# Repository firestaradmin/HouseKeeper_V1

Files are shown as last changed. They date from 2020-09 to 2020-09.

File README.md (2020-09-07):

@[TOC](导航)

---
**本项目已开源至GitHub：*[点我传送](https://github.com/firestaradmin/HouseKeeperV1)***

---
# 一、HouseKeeperV1.0介绍
### 1.项目简介：

 - HouseKeeper_V1.0  是一款智能物联家居产品，它可以根据需求方便的扩展各种家居家电控制，例如门的控制，窗帘的控制，和一些其他家电的控制，只需要简单外接一个继电器便可。本次我们将用指纹门锁控制，来阐述HouseKeeper的功能。
### 2.项目图片外观实例：
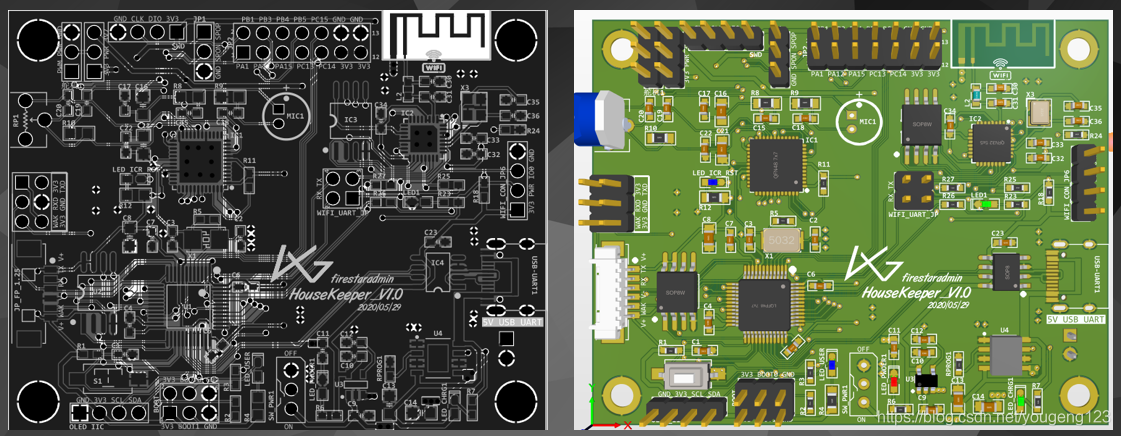
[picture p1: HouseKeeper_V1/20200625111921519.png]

##### · 初步产品图如下
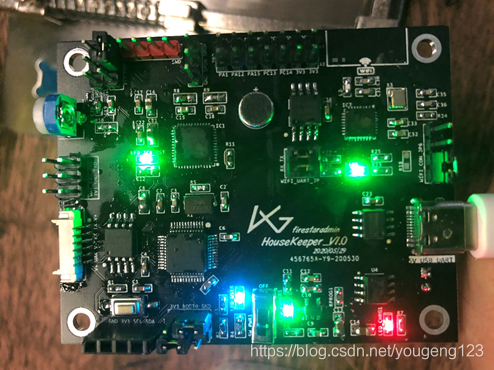
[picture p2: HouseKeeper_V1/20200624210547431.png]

##### · 指纹门锁实例图
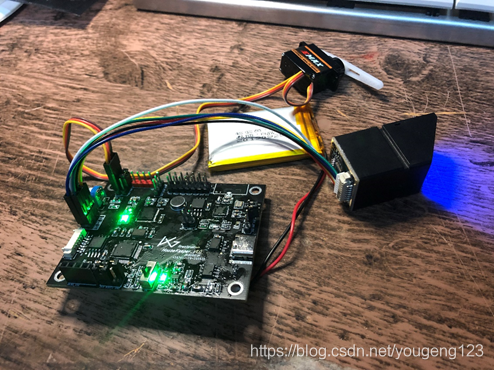
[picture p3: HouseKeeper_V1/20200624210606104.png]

### 3.项目板载资源及功能介绍：
 - 本次项目PCB使用STM32F103C8T6作为主控芯片，板载了WIFI和LD3320语音识别芯片。 有板载麦克风，和0.5W的扬声器输出。
   PCB周边具有舵机接口，指纹模块接口，和将近十个IO扩展，可方便的扩展其他应用。
   另外Type-C的usb串口供电二合一，很方便产品开发阶段使用。

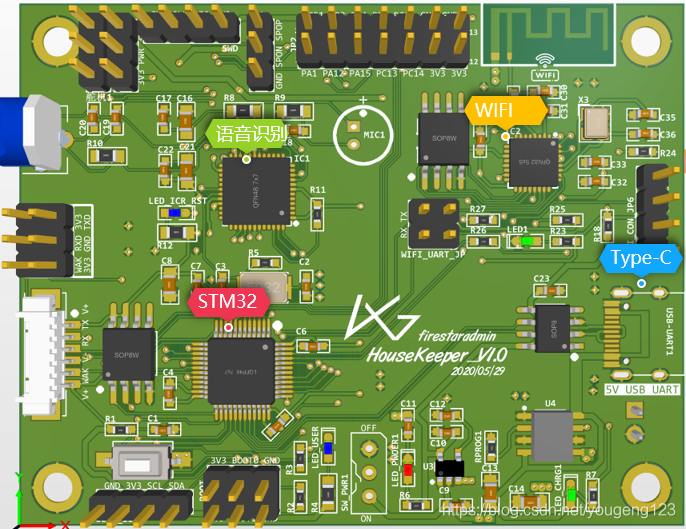
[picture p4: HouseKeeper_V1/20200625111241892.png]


 - 板载资源：
MCU：STM32F103
SPI-FLASH：	W25Q64-8MB
WIFI：ESP8266EX
语音识别： LD3320
锂电池电源管理：TP4056
等等

# 二、HouseKeeperV1.0部分原理图
### 1.主控部分：
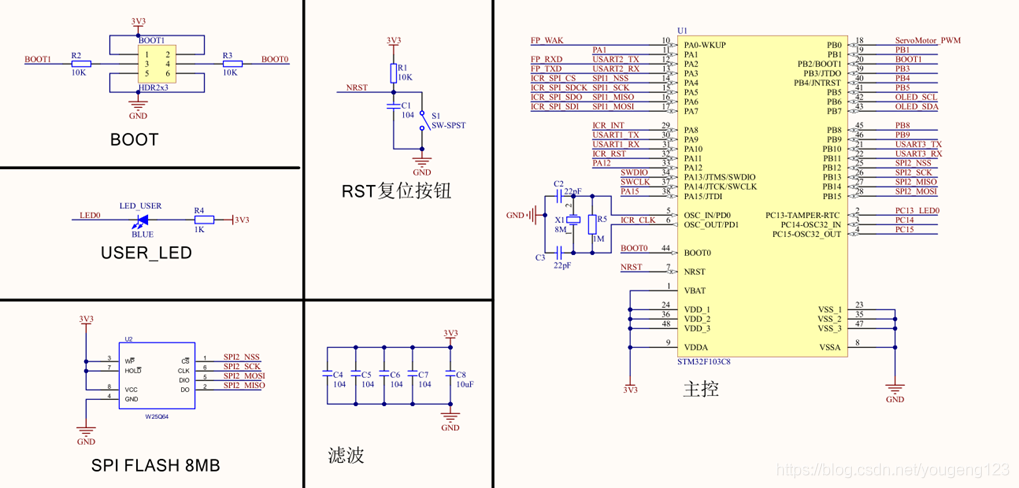
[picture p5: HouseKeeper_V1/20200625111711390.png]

### 2.ESP8266EX-WIFI部分：
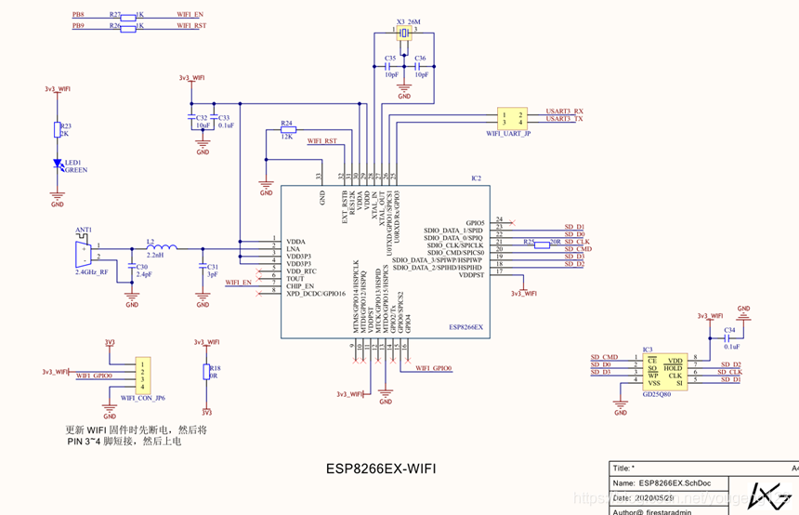
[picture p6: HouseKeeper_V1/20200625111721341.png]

### 3.LD3320语音识别部分：
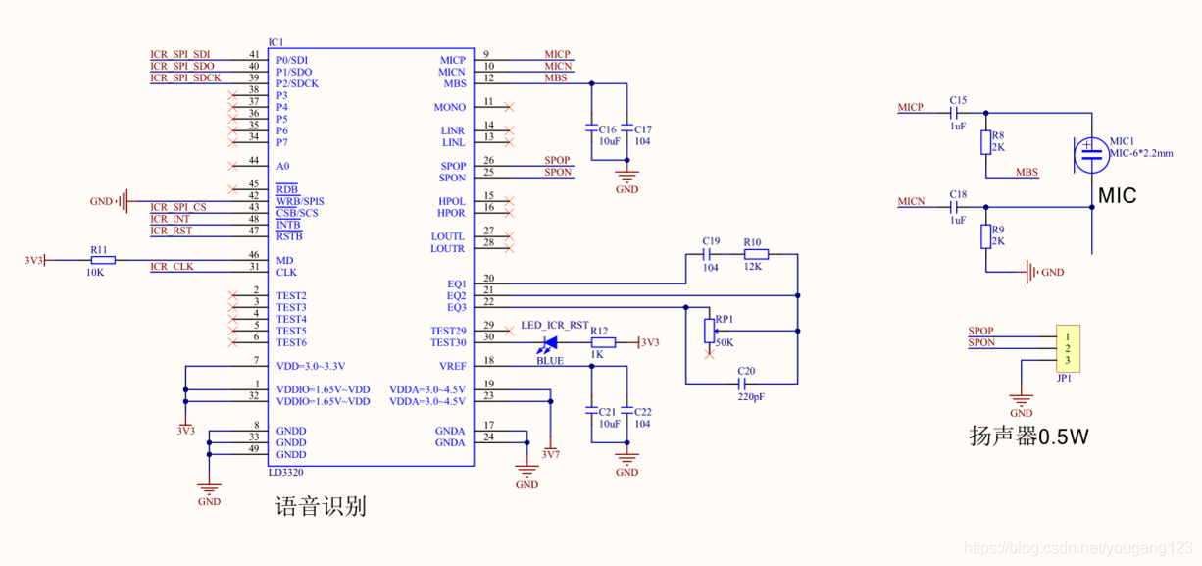
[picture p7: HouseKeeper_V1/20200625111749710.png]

# 三、基于HouseKeeperV1.0的案例-物联网指纹门锁

 - 程序会识别指纹id，判断是谁开了门，并且实时更新到云服务器上的数据库中。 QT中可以实时查看到服务器数据库的信息。

### 1.基础流程图：
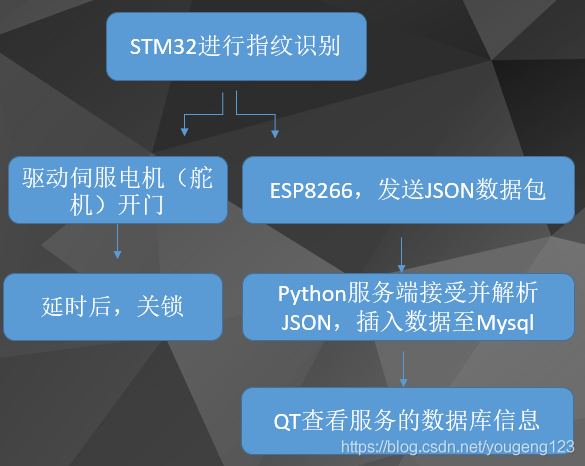
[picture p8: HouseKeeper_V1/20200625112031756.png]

### 2.软件部分框架：
 - 主控程序使用keil编写STM32—C程序
 - WIFI固件，采用arduino编写C++程序
 - 服务器后台使用Python编写SOCKET TCP服务程序
 - 服务器部署了Mysql数据库用于记录开门信息
 - 上位机查看数据库使用QT-C++编写
##### 1.ESP8266WIFI固件功能：
 - 首先连接指定WIFI，循环检查连接状态 如果接受到了，主控发送来的指纹ID，说明该ID开了门 
 - 使用socket连接服务器Serve端。 发送指定格式的JSON数据包，根据ID识别是某位开的门，上传不同的信息

 - **JSON数据包格式：”{“opreation”:“close”, “Note”:“firestaradmin”}”**
##### 2.Python服务端功能：

 - 使用socket 建立TCP服务器，等待Client的连接。
 - 如果有数据接收到，就进行JSON解析，如果正确，无缺失内容，则和系统时间，一起插入至Mysql数据库。
 - 接受客户端发送JSON数据包并解析，解析成功后讲数据插入Mysql数据库

### 3.实例开发过程的一些图片：
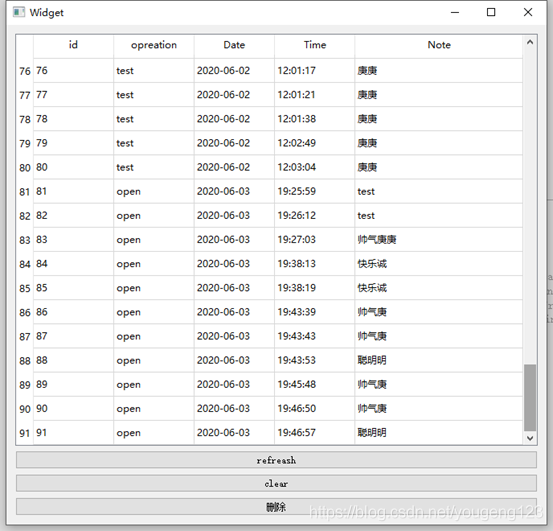
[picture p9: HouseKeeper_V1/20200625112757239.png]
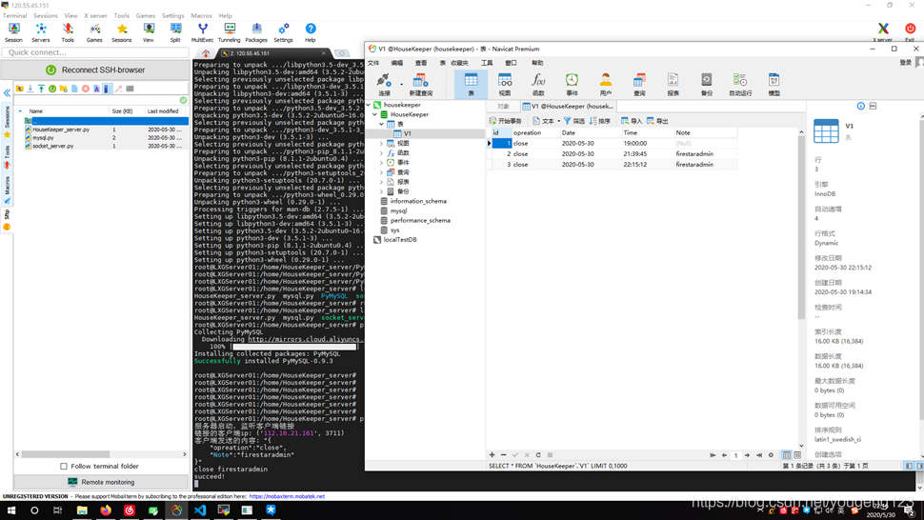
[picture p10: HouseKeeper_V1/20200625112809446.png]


 - 具体演示视频已上传至GitHub项目文件下的report文件夹下，可一起下载后观看

# 四、制作过程部分图片
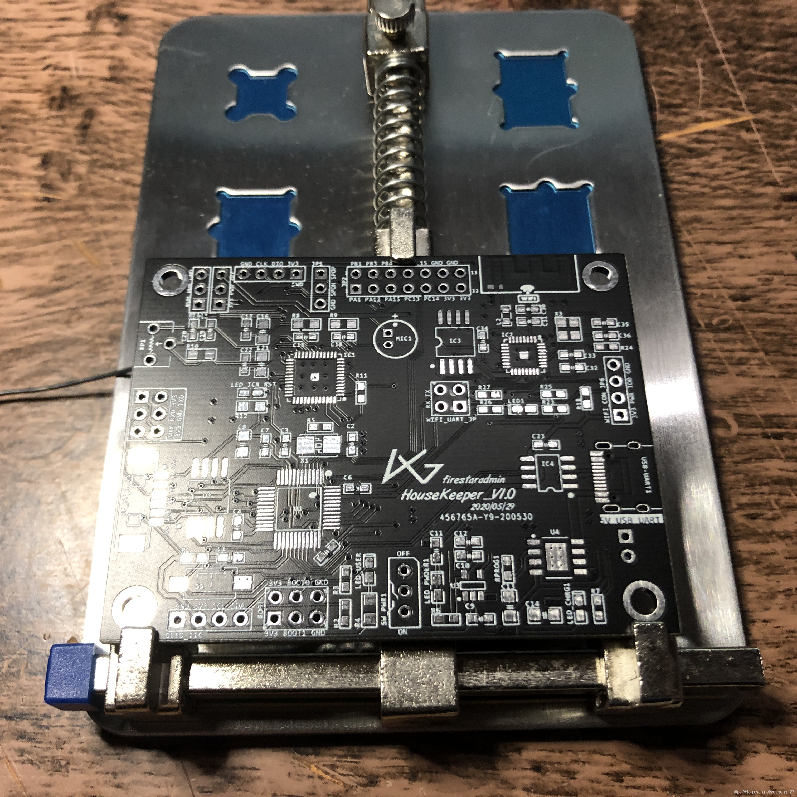
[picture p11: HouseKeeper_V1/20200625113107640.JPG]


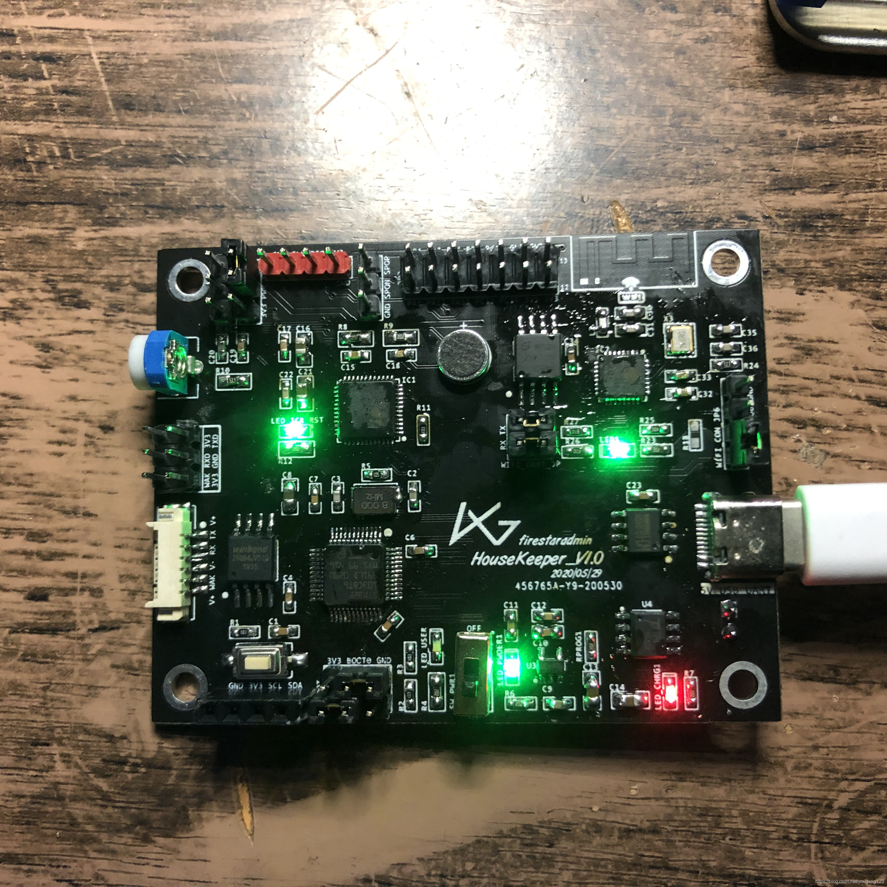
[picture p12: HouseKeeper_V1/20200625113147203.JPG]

在这里插入图片描述
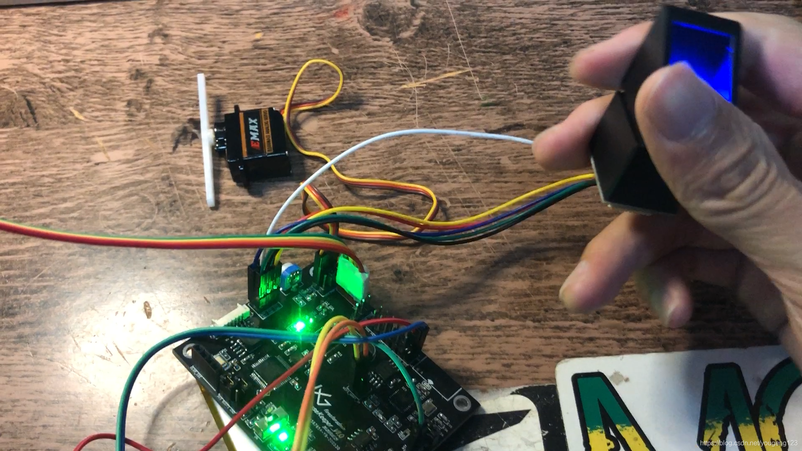
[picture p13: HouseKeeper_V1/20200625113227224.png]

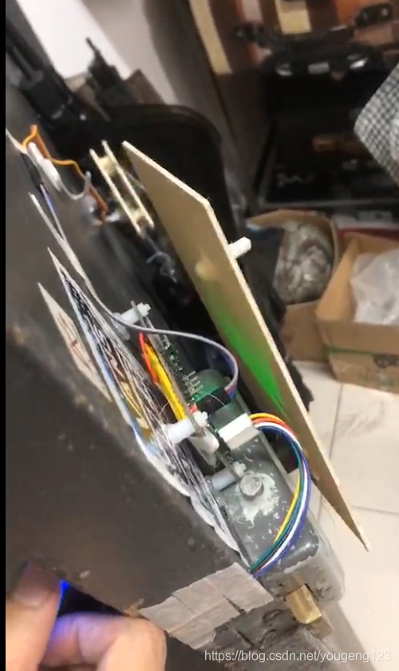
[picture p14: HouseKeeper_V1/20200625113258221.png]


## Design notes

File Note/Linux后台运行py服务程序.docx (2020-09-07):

## &符号

这两天要在服务器端一直运行一个Python脚本，当然就想到了在命令后面加&符号
$ python /data/python/server.py >python.log &

说明：
1、 > 表示把标准输出（STDOUT）重定向到 那个文件，这里重定向到了python.log
2、 & 表示在后台执行脚本
这样可以到达目的，但是，我们退出shell窗口的时候，必须用exit命令来退出，否则，出之后，该进程也会随着shell的消失而消失（退出、关闭）

## 使用nohup(not hang up)

$ nohup python /data/python/server.py > python.log3 2>&1 &

说明：
1、1是标准输出（STDOUT）的文件描述符，2是标准错误（STDERR）的文件描述符
1> python.log 简化为 > python.log，表示把标准输出重定向到python.log这个文件
2、2>&1 表示把标准错误重定向到标准输出，这里&1表示标准输出
为什么需要将标准错误重定向到标准输出的原因，是因为标准错误没有缓冲区，而STDOUT有。
这就会导致 commond > python.log 2> python.log 文件python.log被两次打开，而STDOUT和 STDERR将会竞争覆盖，这肯定不是我门想要的
3、好了，我们现在可以直接关闭shell窗口（我用的是SecureCRT，用的比较多的还有Xshell），而不用再输入exit这个命令来退出shell了

command &让进程在后台运行

jobs 查看后台运行的进程

fg %n 让后台运行的进程n到前台来

bg %n 让进程n到后台去

kill %n 杀死job

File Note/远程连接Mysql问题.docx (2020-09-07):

## Mysql 监听ip地址修改

Mysql默认在本地环路地址127.0.0.1的3306端口监听，要使用其它IP地址需要修改配置文件。

1.编辑/etc/my.cnf 在[mysqld]节中增加下面一行：

bind-address=0.0.0.0 #全部地址或者指定的ip地址

2.重启服务

service mysqld restart

3.验证

netstat -tln

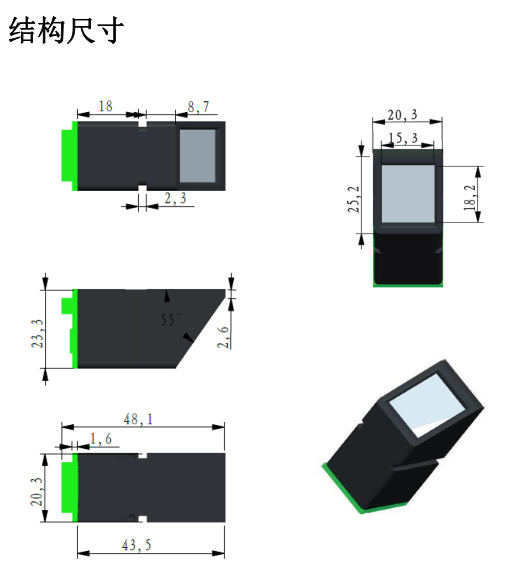
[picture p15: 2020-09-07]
DOC/YX66318-AS608指纹模块-190520/结构图.png

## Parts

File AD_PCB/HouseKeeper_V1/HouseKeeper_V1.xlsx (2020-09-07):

Comment | Description | Designator | Footprint | Quantity
104 | Capacitor, 无极性贴片电容 | C1, C4, C5, C6, C7, C10, C17, C19, C22 | C 0603_M | 9
10uF | 无极性贴片电容, Capacitor | C8, C13, C14, C16, C21 | C 0805_M | 5
1K | 贴片电阻, Resistor | R6, R7, R26, R27 | R 0603_M | 4
10K |  | R1, R2, R3, R11 | R 0603_M | 4
Comment |  | Designator1, Designator10 | M3 125X200 | 4
0.1uF | 无极性贴片电容 | C23, C33, C34 | C 0603_M | 3
HDR-1X3 | 3P接插件 | JP1, JP3, 舵机1 | HDR2.54-LI-3P | 3
1K | 贴片电阻 | R4, R12 | R 0805_M | 2
1uF | 无极性贴片电容 | C15, C18 | C 0603_M | 2
2K | Resistor | R23, RPROG1 | R 0603_M | 2
2K | 贴片电阻 | R8, R9 | R 0805_M | 2
10pF | 无极性贴片电容 | C35, C36 | C 0603_M | 2
22pF | Capacitor | C2, C3 | C 0603_M | 2
105 | Capacitor | C9, C11 | C 0603_M | 2
BLUE | 贴片LED | LED_ICR_RST, LED_USER | LED 0603B | 2
0R | Resistor | R18 | R 0603_M | 1
1M | 贴片电阻 | R5 | R 0603_M | 1
2.2nH | 小功率贴片电感 | L2 | L 0603 | 1
2.4GHz_RF |  | ANT1 | ANT-F-1-2.4G | 1
2.4pF | 无极性贴片电容 | C30 | C 0603_M | 1
3pF | 无极性贴片电容 | C31 | C 0603_M | 1
8M | Crystal Oscillator | X1 | OSC 5032-2P | 1
10uF | 无极性贴片电容 | C32 | C 0603_M | 1
12K | Resistor | R24 | R 0603_M | 1
12K | 贴片电阻 | R10 | R 0805_M | 1
20R | Resistor | R25 | R 0603_M | 1
22nf | Capacitor | C12 | C 0603_M | 1
26M | 4脚无源晶振 | X3 | OSC 3225-4P | 1
50K | 插件单联电位器 | RP1 | 3306W | 1
220pF | 无极性贴片电容 | C20 | C 0603_M | 1
CH340N | USB 转串口芯片 CH330/CH340N | IC4 | SOP8_N | 1
ESP8266EX | WIFI-芯片 | IC2 | QFN32 5x5_M | 1
GD25Q80 | 外置Flash | IC3 | SOP8W_N | 1
GREEN | 贴片LED | LED1 | LED 0603G | 1
HDR1x2 | Connector | 4.2V锂电池 | XH2.54-LI-2P | 1
HDR2x3 | Connector | BOOT | HDR2.54-LI-2x3P | 1
HDR-1X4 | 4P接插件 | WIFI_CON_JP6 | HDR2.54-LI-4P | 1
HDR-1X6 | 6P接插件 | JP_FP_1.25 | MX 1.25-WS-6P | 1
HDR-1X6 | 6P接插件 | JP_FP_2.54 | HDR2.54-LI-2x3P | 1
Header2X2 | 2*2P接插件 | WIFI_UART_JP | HDR2.54-LI-2x2P | 1
Header 2X7 | 7*2P接插件 | JP2 | HDR2.54-LI-2x7P | 1
LD3320 | LD3320 芯片是一款“ 语音识别”专用芯片，由 ICRoute 公司设计生产。该芯 片集成了语音识别处理器和一些外部电路，包括 AD、DA 转换器、麦克风接口、 声音输出接口等。本芯片在设计上注重节能与高效，不需要外接任何的辅助芯片 如 Flash、RAM 等，直接集成在现有的产品中即可以实现语音识别/声控/人机对 话功能。并且，识别的关键词语列表是可以任意动态编辑的。 | IC1 | QFN48 7X7_M | 1
LED | LED | LED_CHRG1 | LED 0603G | 1
MIC-6*2.2mm | 电容麦克风 | MIC1 | MIC-6*2.2MM | 1
OLED | Header, 4-Pin | OLED_IIC | HDR2.54-LI-4P | 1
RED | 贴片LED | LED_PWOER1 | LED 0603R | 1
RT9193 |  | U3 | SOT-23-5 | 1
STM32F103C8 | Flaah:64/RAM:20/IO:36 | U1 | LQFP48 7X7_M | 1
SWD | Header, 4-Pin | SWD | HDR2.54-LI-4P | 1
SWITCH-SPST | Switch | SW_PWR1 | Switch_3p_2.5mmjianju | 1
SW-SPST | Single-Pole, Single-Throw Switch | S1 | TSW SMD-3*6*2.5 | 1
TP4056 |  | U4 | ESOP8 | 1
Type-C |  | USB-UART1 | TYPE-C | 1
W25Q64 |  | U2 | SOP8W_M | 1

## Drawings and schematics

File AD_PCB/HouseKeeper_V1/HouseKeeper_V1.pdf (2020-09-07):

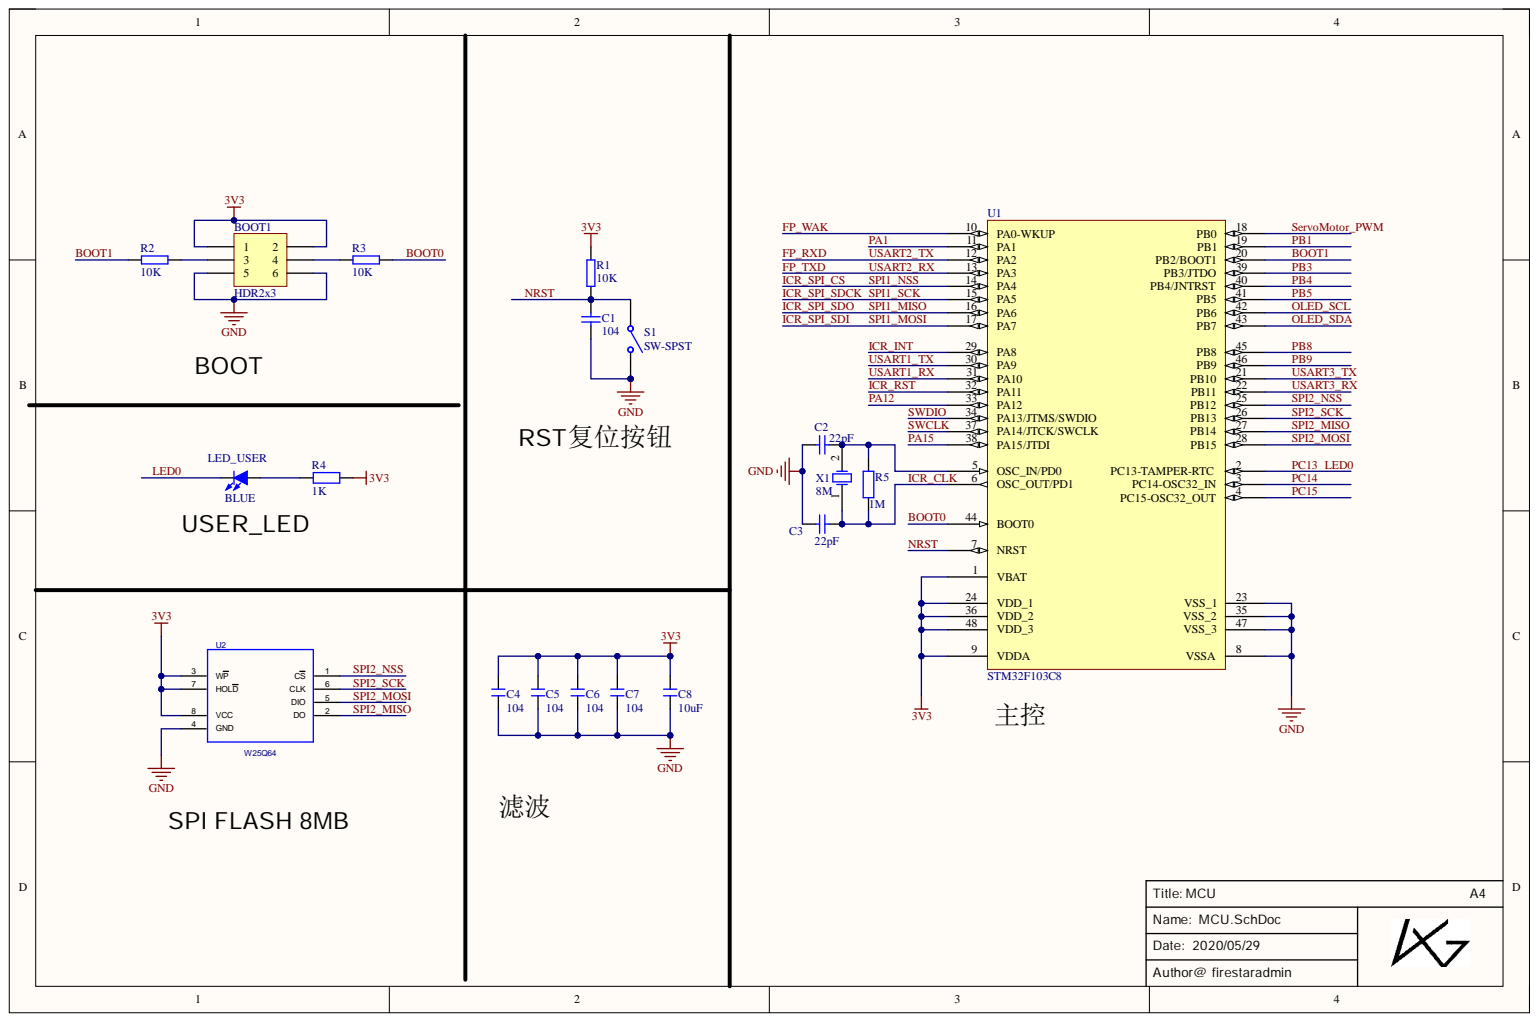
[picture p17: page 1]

ICR_CL K 6

2 4
3 6 | 3 5
4 8 | | 4 7

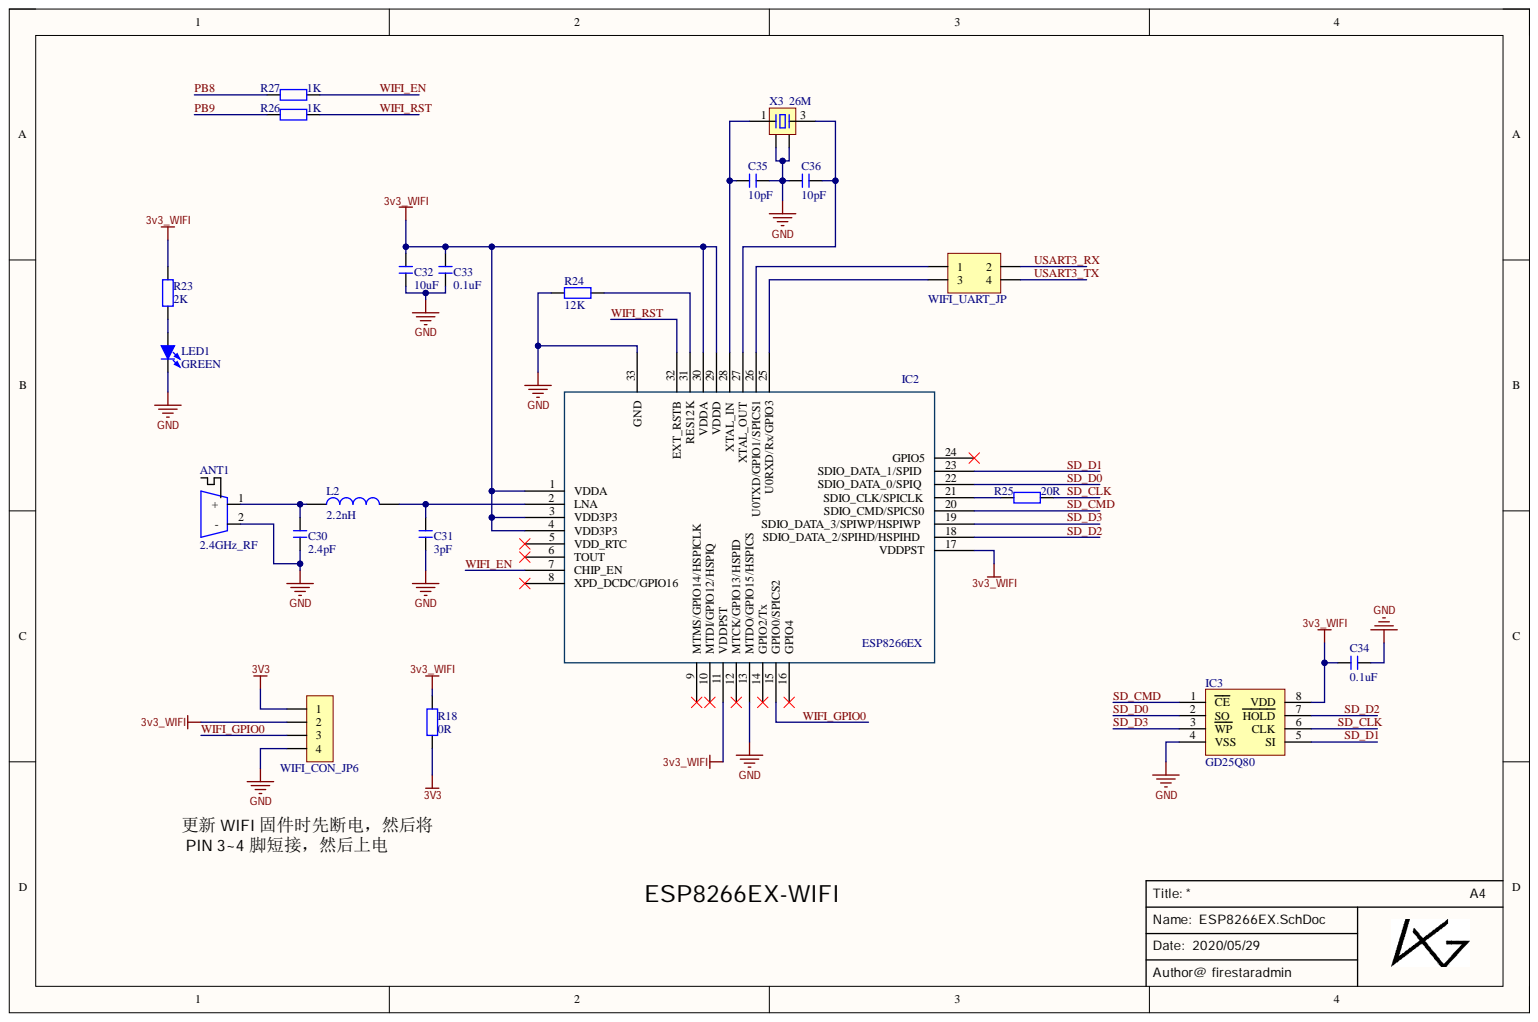
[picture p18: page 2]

更新 WIFI 固件时先断电，然后将
PIN 3~4 脚短接，然后上电

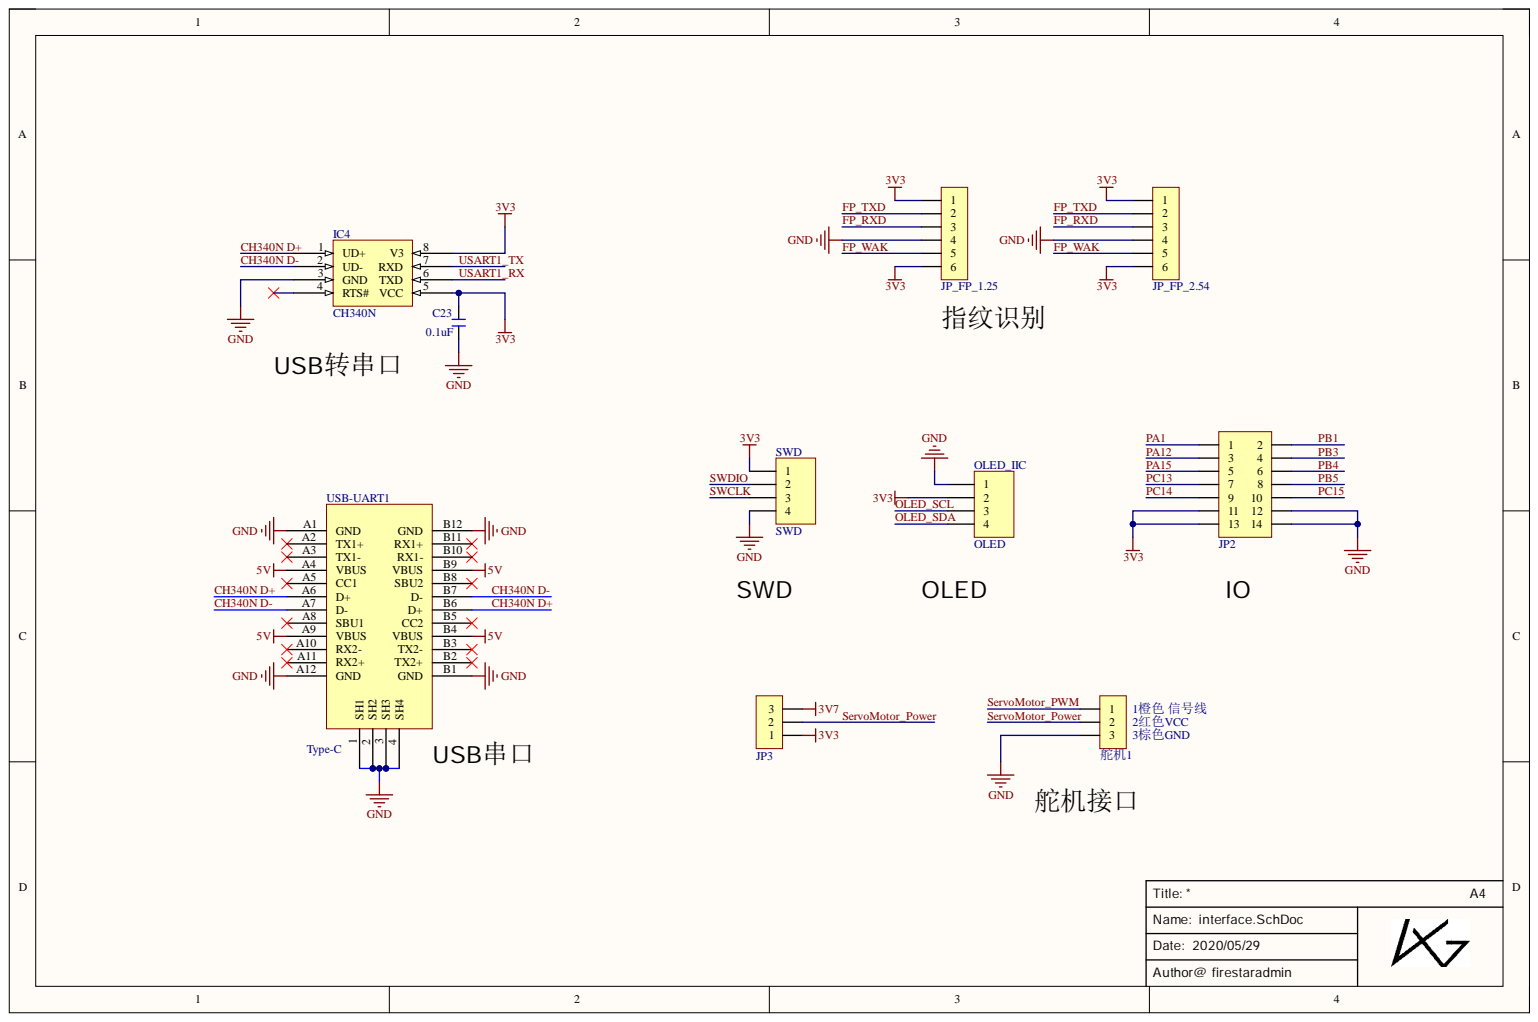
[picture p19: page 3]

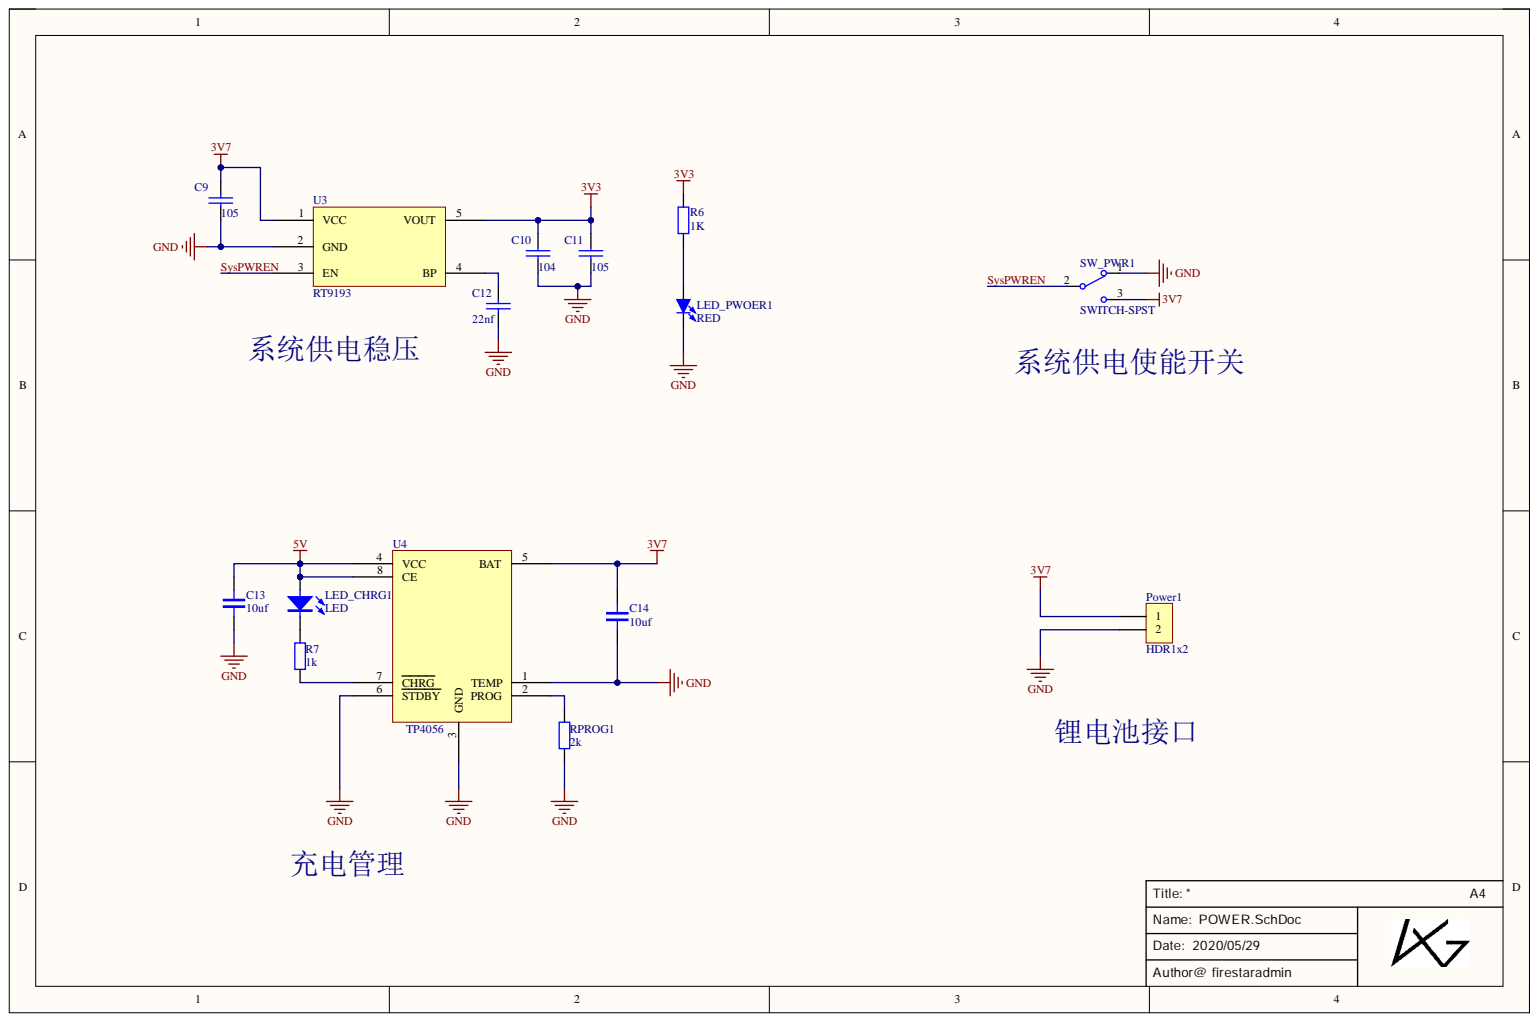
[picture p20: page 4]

STDBY 6

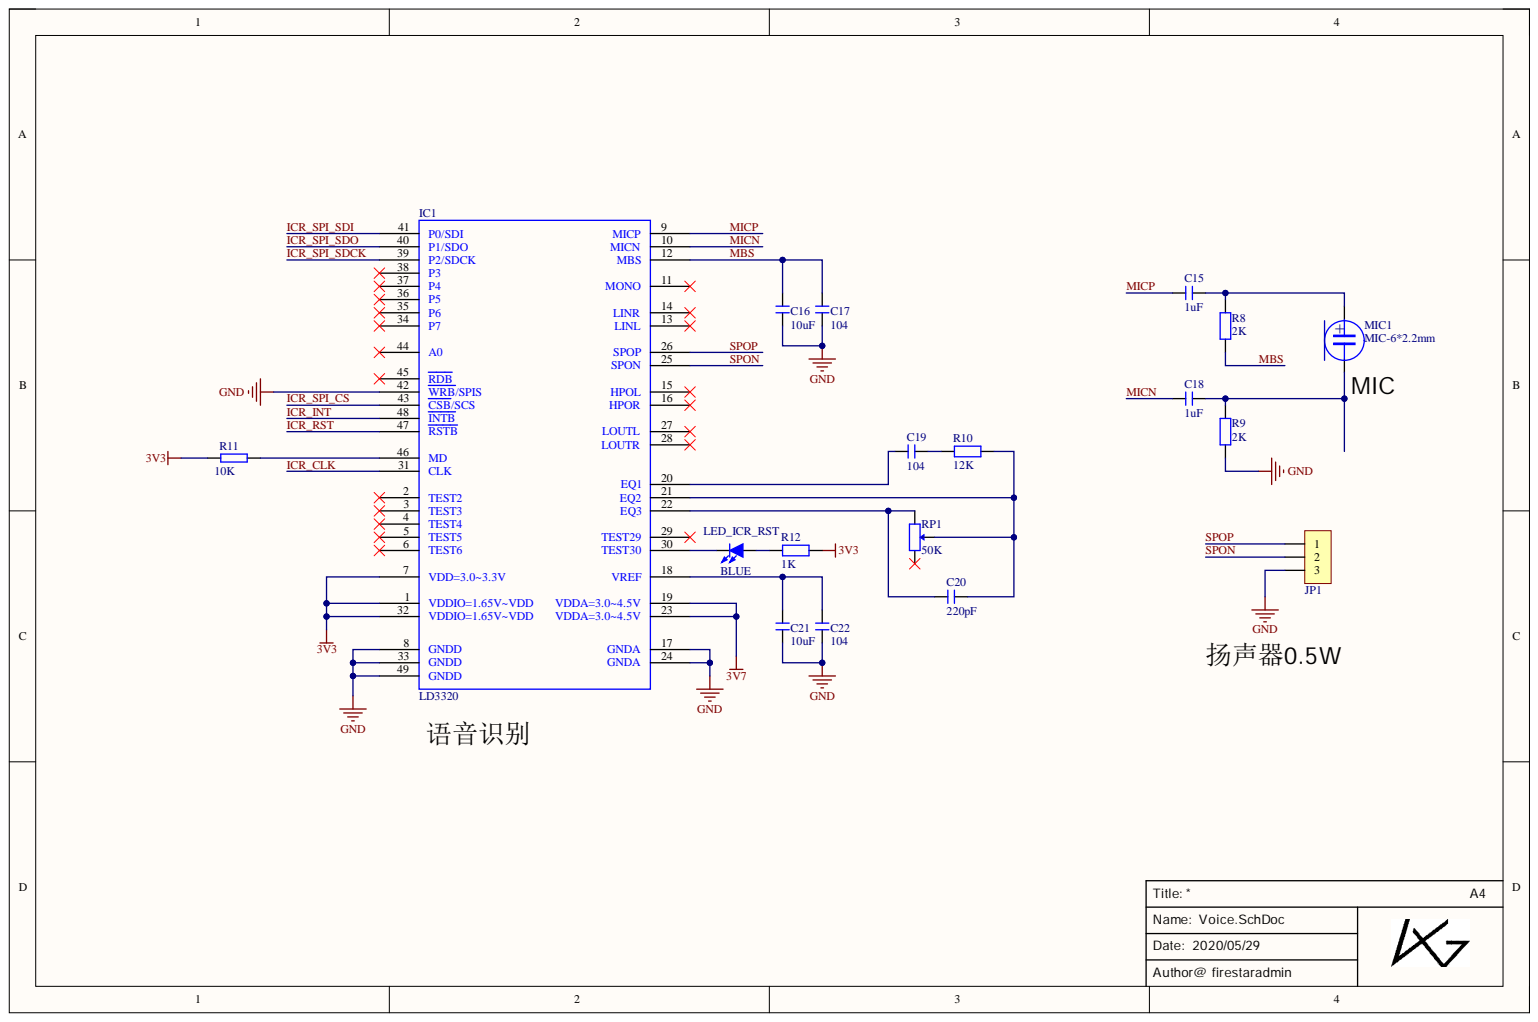
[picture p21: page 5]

1 | 1 9
3 2 | 2 3

3 3 | 2 4
4 9

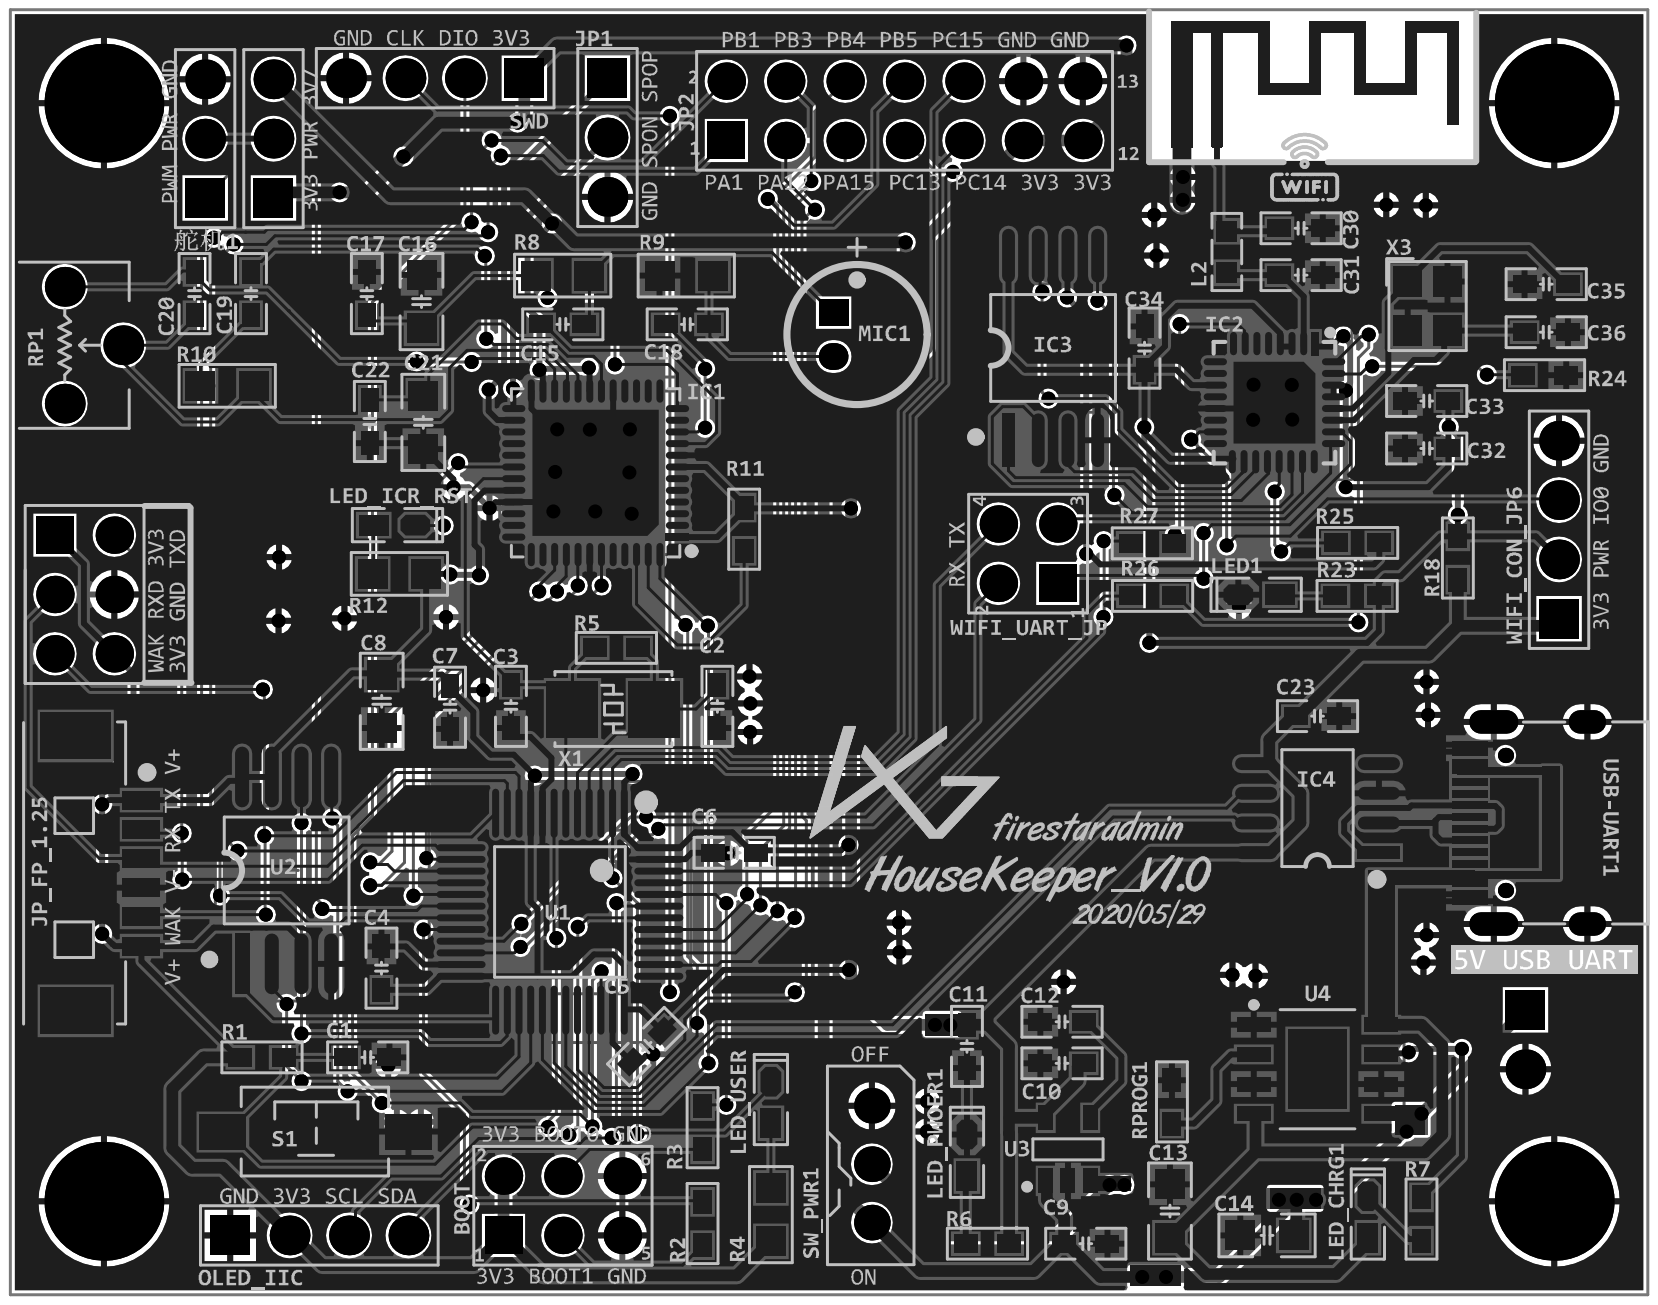
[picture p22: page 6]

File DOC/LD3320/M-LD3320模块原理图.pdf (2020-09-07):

# MIC Input

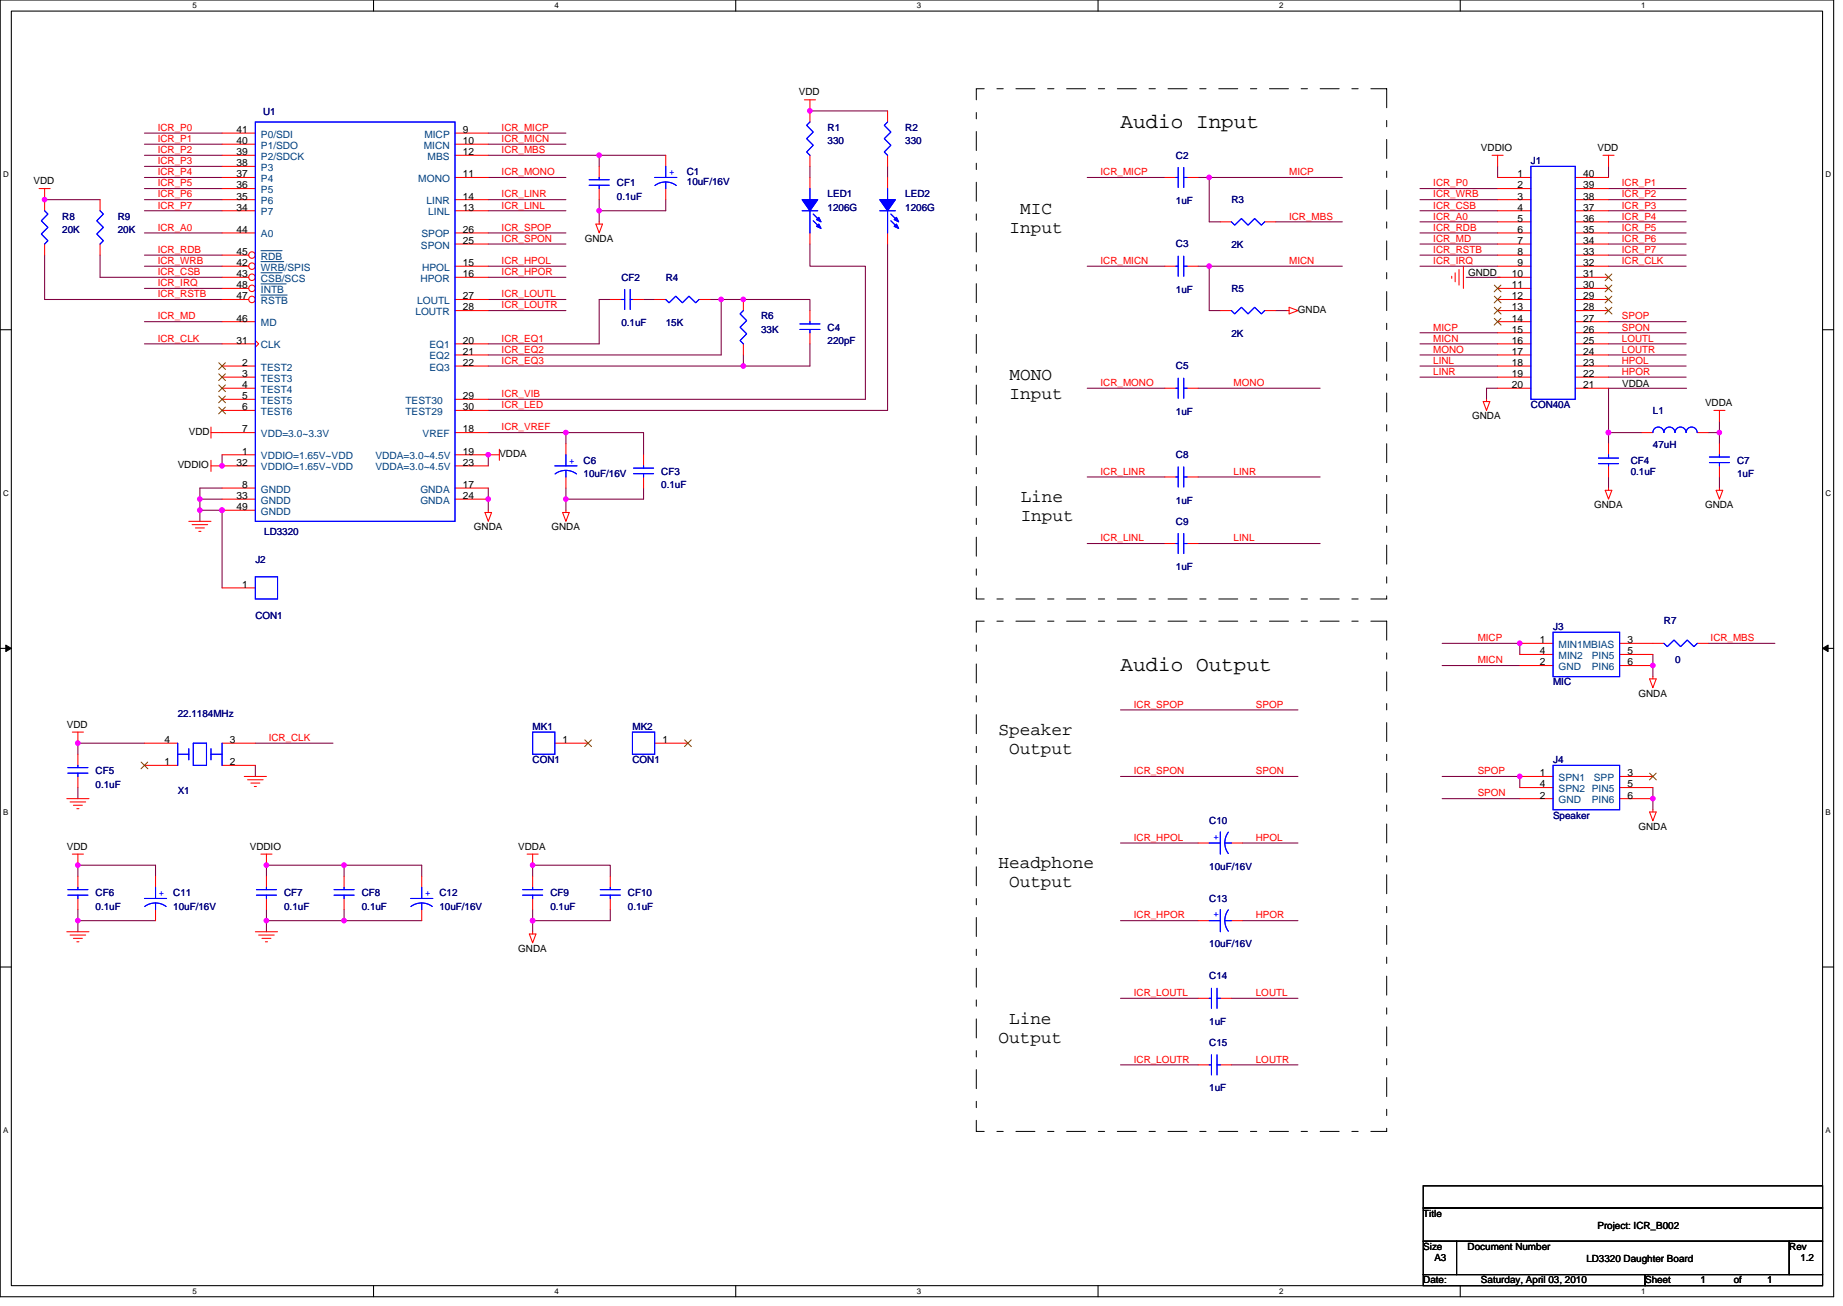
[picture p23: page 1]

Size Size Size A3 A3 A3 | Document Number Document Number Document Number LD3320 Daughter Board LD3320 Daughter Board LD3320 Daughter Board | Rev Rev Rev 1.2 1.2 1.2

Date: Date: Date: Saturday, April 03, 2010 Saturday, April 03, 2010 Saturday, April 03, 2010 | Sheet Sheet Sheet 1 1 1 of of of 1 1 1

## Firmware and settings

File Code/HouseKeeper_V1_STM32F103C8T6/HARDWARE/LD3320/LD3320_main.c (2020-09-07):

/***************************乐声电子科技有限公司****************************
**  工程名称：YS-V0.4语音识别开发板程序
**	CPU: STM32f103RCT6
**	晶振：8MHZ
**	波特率：9600 bit/S
**	配套产品信息：YS-V0.4语音识别开发板
**                http://yuesheng001.taobao.com
**  作者：zdings
**  联系：751956552@qq.com
**  修改日期：2012.4.11
**  说明：本程序 具备语音识别、串口通信、开发板基本功能演示。
***************************乐声电子科技有限公司******************************/
#include "reg_rw.h"

/*************端口信息********************
 * 接线说明
 * RST      PB6
 * CS   	PB8
 * WR/SPIS  PB9
 * P2/SDCK  PB3
 * P1/SDO   PB4
 * P0/SDI   PB5
 * IRQ      PC1
 * A0				PB7
 * RD       PA0
*****************************************/



/************************************************************************************
//	nAsrStatus 用来在main主程序中表示程序运行的状态，不是LD3320芯片内部的状态寄存器
//	LD_ASR_NONE:		表示没有在作ASR识别
//	LD_ASR_RUNING：		表示LD3320正在作ASR识别中
//	LD_ASR_FOUNDOK:		表示一次识别流程结束后，有一个识别结果
//	LD_ASR_FOUNDZERO:	表示一次识别流程结束后，没有识别结果
//	LD_ASR_ERROR:		表示一次识别流程中LD3320芯片内部出现不正确的状态
*********************************************************************************/
uint8 nAsrStatus=0;	

void LD3320_Init(void);



void LD3320_EXTI_Cfg(void);
void LD3320_Spi_cfg(void);
void LD3320_GPIO_Cfg(void);
void LED_gpio_cfg(void);

/***********************************************************
* 名    称： LD3320_main(void)
* 功    能： 主函数LD3320程序入口
* 入口参数：  
* 出口参数：
* 说    明：
* 调用方法： 
**********************************************************/ 

void  LD3320_main(void)
{
	uint8 nAsrRes=0;
	LD3320_Init();	  
	nAsrStatus = LD_ASR_NONE;		//	初始状态：没有在作ASR
	while(1)
	{
// 	switch(nAsrStatus)
//		{
//			case LD_ASR_RUNING:
//			case LD_ASR_ERROR:		
//												break;
//			case LD_ASR_NONE:
//											nAsrStatus=LD_ASR_RUNING;
//											if (RunASR()==0)	//	启动一次ASR识别流程：ASR初始化，ASR添加关键词语，启动ASR运算
//											{		
//												nAsrStatus = LD_ASR_ERROR;
//											}
//											break;
//
//			case LD_ASR_FOUNDOK:
//											 nAsrRes = LD_GetResult( );	//	一次ASR识别流程结束，去取ASR识别结果										 					
//												 switch(nAsrRes)		   /*对结果执行相关操作,客户修改*/
//												  {
//													  case CODE_LSD:			/*命令“流水灯”*/
//															PrintCom(USART1,"“流水灯”命令识别成功\r\n"); /*text.....*/
//																						 break;
//														case CODE_SS:	 /*命令“闪烁”*/
//															PrintCom(USART1,"“闪烁”命令识别成功\r\n"); /*text.....*/
//																						 break;
//														case CODE_AJCF:		/*命令“按键触发”*/
//												
//															PrintCom(USART1,"“按键触发”命令识别成功\r\n"); /*text.....*/
//																						break;
//														case CODE_QM:		/*命令“全灭”*/
//												
//															PrintCom(USART1,"“全灭”命令识别成功\r\n"); /*text.....*/
//																						break;
//														default:break;
//													}	
//												nAsrStatus = LD_ASR_NONE;
//											break;
//			
//			case LD_ASR_FOUNDZERO:
//			default:
//								nAsrStatus = LD_ASR_NONE;
//								break;
			}//switch
	}// while


/***********************************************************
* 名    称：LD3320_Init(void)
* 功    能：模块驱动端口初始配置
* 入口参数：  
* 出口参数：
* 说    明：
* 调用方法： 
**********************************************************/ 
void LD3320_Init(void)
{
	LD3320_GPIO_Cfg();	
	LD3320_Spi_cfg();	 
	LD_reset();
}

/***********************************************************
* 名    称： void Delay_( int i)
* 功    能： 短延时
* 入口参数：  
* 出口参数：
* 说    明：
* 调用方法： 
**********************************************************/ 
void Delay_( int i)
 {     
    while( i--)
       {	

        }
 }	
/***********************************************************
* 名    称：	LD3320_delay(unsigned long uldata)
* 功    能：	长延时函数
* 入口参数：  
* 出口参数：
* 说    明：
* 调用方法： 
**********************************************************/ 
 void  LD3320_delay(u16 ms)
{
//	unsigned int j  =  0;
//	unsigned int g  =  0;
//	for (j=0;j<10;j++)
//	{
//		for (g=0;g<uldata;g++)
//		{
//			Delay_(1080);
//		}
//	}
   delay_us(120*ms);
}

/***********************************************************
* 名    称：	RunASR(void)
* 功    能：	运行ASR
* 入口参数：  
* 出口参数：
* 说    明：
* 调用方法： 
**********************************************************/ 
uint8 RunASR(void)
{
	uint8 i=0;
	uint8 asrflag=0;
	for (i=0; i<5; i++)			//	防止由于硬件原因导致LD3320芯片工作不正常，所以一共尝试5次启动ASR识别流程
	{
		LD_AsrStart();			//初始化ASR
		delay_ms(100);
		if (LD_AsrAddFixed()==0)	//添加关键词语到LD3320芯片中
		{
			LD_reset();			//	LD3320芯片内部出现不正常，立即重启LD3320芯片
			delay_ms(100);			//	并从初始化开始重新ASR识别流程
			continue;
		}
		delay_ms(10);
		if (LD_AsrRun() == 0)
		{
			LD_reset();			//	LD3320芯片内部出现不正常，立即重启LD3320芯片
			delay_ms(100);			//	并从初始化开始重新ASR识别流程
			continue;
		}
    LD_ReadReg(0xbf);
		asrflag=1;
		break;					//	ASR流程启动成功，退出当前for循环。开始等待LD3320送出的中断信号
	}

	return asrflag;
}

/***********************************************************
* 名    称：LD3320_GPIO_Cfg(void)
* 功    能：初始化需要用到的IO口
* 入口参数：  
* 出口参数：
* 说    明：
* 调用方法： 
**********************************************************/ 
void LD3320_GPIO_Cfg(void)
{	
	  GPIO_InitTypeDef GPIO_InitStructure;
	 	RCC_APB2PeriphClockCmd( RCC_APB2Periph_GPIOC,ENABLE);
		/*PC0:MODE, PC1:RSTB, PC2:WR*/
		GPIO_InitStructure.GPIO_Pin =GPIO_Pin_0|GPIO_Pin_0|GPIO_Pin_2;//;
		GPIO_InitStructure.GPIO_Speed = GPIO_Speed_50MHz;
		GPIO_InitStructure.GPIO_Mode = GPIO_Mode_Out_PP;
		GPIO_Init(GPIOC,&GPIO_InitStructure);
    
		GPIO_SetBits(GPIOC,GPIO_Pin_0);	/*MODE默认拉高  选择SPI*/
    GPIO_ResetBits(GPIOC,GPIO_Pin_2);	/*WR默认拉低*/
	 
}
/***********************************************************
* 名    称：LD3320_Spi_cfg(void)
* 功    能：配置SPI功能和端口初始化
* 入口参数：  
* 出口参数：
* 说    明：
* 调用方法： 
**********************************************************/ 
void LD3320_Spi_cfg(void)
{
	SPI_InitTypeDef  SPI_InitStructure;
	GPIO_InitTypeDef GPIO_InitStructure;
	RCC_APB1PeriphClockCmd(RCC_APB1Periph_SPI2,ENABLE);	   //使能SPI2外设时钟
  RCC_APB2PeriphClockCmd(RCC_APB2Periph_GPIOB|RCC_APB2Periph_AFIO,ENABLE);
//  GPIO_PinRemapConfig(GPIO_Remap_SWJ_JTAGDisable, ENABLE); 

	/*P0/P1/P2*/
	GPIO_InitStructure.GPIO_Pin = GPIO_Pin_13 | GPIO_Pin_14 | GPIO_Pin_15;
	GPIO_InitStructure.GPIO_Speed = GPIO_Speed_50MHz;
	GPIO_InitStructure.GPIO_Mode = GPIO_Mode_AF_PP;
	GPIO_Init(GPIOB,&GPIO_InitStructure);
  GPIO_SetBits(GPIOB,GPIO_Pin_13 | GPIO_Pin_14 | GPIO_Pin_15);

	GPIO_InitStructure.GPIO_Pin = GPIO_Pin_12;			//CS(NSS)
	GPIO_InitStructure.GPIO_Speed = GPIO_Speed_50MHz;
	GPIO_InitStructure.GPIO_Mode = GPIO_Mode_Out_PP;
	GPIO_Init(GPIOB, &GPIO_InitStructure);
  
	LD_CS_H();

	/* SPI2 配置 */
  SPI_Cmd(SPI2, DISABLE);	
	SPI_InitStructure.SPI_Direction = SPI_Direction_2Lines_FullDuplex;  //全双工
	SPI_InitStructure.SPI_Mode = SPI_Mode_Master;				                //主模式
	SPI_InitStructure.SPI_DataSize = SPI_DataSize_8b;					          //8位
	SPI_InitStructure.SPI_CPOL = SPI_CPOL_High;						              //时钟极性 空闲状态时，SCK保持高电平
	SPI_InitStructure.SPI_CPHA = SPI_CPHA_1Edge;						   //时钟相位 数据采样从第一个时钟边沿开始
	SPI_InitStructure.SPI_NSS = SPI_NSS_Soft;							   //软件产生NSS
	SPI_InitStructure.SPI_BaudRatePrescaler = SPI_BaudRatePrescaler_32;   //波特率控制 SYSCLK/128
	SPI_InitStructure.SPI_FirstBit = SPI_FirstBit_MSB;				   //数据高位在前
	SPI_InitStructure.SPI_CRCPolynomial = 7;							   //CRC多项式寄存器初始值为7
	SPI_Init(SPI2, &SPI_InitStructure);
	/* 使能SPI2 */
	SPI_Cmd(SPI2, ENABLE);

}
/***********************************************************
* 名    称： LD3320_EXTI_Cfg(void) 
* 功    能： 外部中断功能配置和相关端口配置
* 入口参数：  
* 出口参数：
* 说    明：
* 调用方法： 
**********************************************************/ 
void LD3320_EXTI_Cfg(void)
{

}


/***********************************************************
* 名    称：  EXTI1_IRQHandler(void)
* 功    能： 外部中断函数
* 入口参数：  
* 出口参数：
* 说    明：
* 调用方法： 
**********************************************************/ 
void EXTI1_IRQHandler(void)
{
	if(EXTI_GetITStatus(EXTI_Line1)!= RESET ) 
	{
 		ProcessInt0(); 
		EXTI_ClearFlag(EXTI_Line1);
		EXTI_ClearITPendingBit(EXTI_Line1);
	}
}

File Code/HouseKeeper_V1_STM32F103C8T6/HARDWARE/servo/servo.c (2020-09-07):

/************************************************************************************
*  Copyright (c), 2020, LXG.
*
* FileName		:
* Author		:firestaradmin
* Version		:1.0
* Date			:
* Description	:
* History		:
*
*
*************************************************************************************/
#include "servo.h"
#include "myTIM.h"

#define SERVO_OPEN  5
#define SERVO_CLOSE 12



void servo_init()
{
	TIM3_PWM_Init(99,14400);	//T = 20ms    50Hz
	TIM_SetCompare3(TIM3,10);
	servo_control(0);
}


void servo_set_compare(u16 value)
{
	
	TIM_SetCompare3(TIM3,value);
}

void servo_control(u8 value)
{
	if(value)
		servo_set_compare(SERVO_OPEN);
	else
		servo_set_compare(SERVO_CLOSE);
}

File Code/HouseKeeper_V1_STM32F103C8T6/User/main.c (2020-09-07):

#include <stm32f10x.h>  
#include "stm32f10x_it.h"
#include "sys.h"
#include "delay.h"
#include "usart.h"
#include "as608.h"
#include "EXTI.h"
#include "myTIM.h"
#include "servo.h"
#include "usmart.h"


u8 FP_id = 0;
u8 FP_Trig_Flag = 0;
u8 servo_Stauts = 0;	//门状态 1：开   0：关

int main()
{
	u8 ensure;
	SystemInit();//晶振时钟初始化
	NVIC_PriorityGroupConfig(NVIC_PriorityGroup_2);//设置中断优先级分组为组2：2位抢占优先级，2位响应优先级
	DelayInit();//延时函数初始化
	uart_init(115200);//串口1初始化
	usart2_init(usart2_baund);//初始化串口2,用于与指纹模块通讯
	usart3_init(115200);//WIFI模块
	PS_StaGPIO_Init();	//初始化FR读状态引脚
	FP_WAK_Init();//指纹中断初始化
	TIM2_Int_Init(100, 7200 - 1); //T = 10ms
	user_led_init();
	//usmart_dev.init(72);
	servo_init();
	

	ensure=PS_ReadSysPara(&AS608Para);  //读AS608模块参数 
	if(ensure==0x00)
	{
		printf("\r\nRemainNum:%d    Level:%d", AS608Para.PS_max-ValidN,AS608Para.PS_level);
	}
	GPIO_SetBits(GPIOC, GPIO_Pin_13);
	//Add_FR();	//录指纹
	while(1)
	{
		
//		DelayMs(100);
//		GPIO_ResetBits(GPIOC, GPIO_Pin_13);
//		DelayMs(100);

		if(FP_WAK_Trig)
		{
			press_FR();
			FP_WAK_Trig = 0;
		}

		if(FP_Trig_Flag)
		{
			GPIO_ResetBits(GPIOC, GPIO_Pin_13);
			servo_control(1);
			servo_Stauts = 1;
			FP_Trig_Flag = 0;
		}
		
	}
}


void user_led_init(void)
{
	RCC_APB2PeriphClockCmd(RCC_APB2Periph_GPIOC,ENABLE);
	GPIO_DeInit(GPIOC);
	
	GPIO_InitTypeDef GPIOType = {
			GPIO_Pin_13,
			GPIO_Speed_50MHz,
			GPIO_Mode_Out_OD
	};
	
	GPIO_Init(GPIOC , &GPIOType);
}



//void WIFI_EN_GPIO_Init(void)
//{
//	RCC_APB2PeriphClockCmd(RCC_APB2Periph_GPIOB,ENABLE);
//	GPIO_InitTypeDef  GPIO_InitStructure;
//	
//	/* RST的IO口设置 */
//	GPIO_InitStructure.GPIO_Pin = GPIO_Pin_8 ;
//	GPIO_InitStructure.GPIO_Mode = GPIO_Mode_Out_PP;		//推挽输出
//	GPIO_InitStructure.GPIO_Speed = GPIO_Speed_50MHz;
//	GPIO_Init(GPIOB, &GPIO_InitStructure);
//	GPIO_SetBits(GPIOB,GPIO_Pin_8);
//	

//}


void WIFI_send_id(u8 id)
{
	u8 buf[3] = {'[',id,']'};
	
	for(int i = 0; i < 3; i++){
		while(USART_GetFlagStatus(USART3,USART_FLAG_TC)==RESET); //循环发送,直到发送完毕   
		USART_SendData(USART3,buf[i]); 
	}
}
